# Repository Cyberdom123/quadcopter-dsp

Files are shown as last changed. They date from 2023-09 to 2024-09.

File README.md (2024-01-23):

# Quadcopter design made from scratch

The goal of the project is to create a working model of a quadcopter UAV, which can be
controlled with a Xbox controller. The project utilises the MPU6050 inertial measurement
unit, which combines MEMS accelerometer and gyroscope into a single IC. The combination of
sensor readings from the IMU combined with an adequate mathematical model and a regulating
system allows to make a quadcopter with a stable control system.



# Quadcopter project implementation

The MCU used in the project implementation is STM32F103C6T6, an ARM Cortex-M3 mi-
crocontroller, containing 32Kbytes of ROM. F1303 has built-in hardware support for I2C and
SPI busses used for data transmission between on-board peripherals.
The MPU6050 has been used as a sensor. It is an inertial measurement unit (IMU), a
MEMS integrated circuit combining in itself an accelerometer and a gyroscope. For easy and
intuitive reading of the sensor data at the code level, a library for initialising and handling the
MPU has been written. It uses the built-in I2C bus which is used to exchange data between the
IMU and MCU. The transmission is made in 400kHz mode. In order to save MCU execution
time, a DMA controller has been used, allowing for sending data from RAM to the peripheral.
Similarly, a library for nRF24L01 radio module has been written. nRF is being used for
digital radio transmission between the UAV and a PC. It is connected to the MCU by the
SPI bus and also uses the DMA mechanism. Another nRF connected to the PC is used to
communicate with the quadcopter. The transceivers are used in order to read telemetry data
and for piloting the UAV using an Xbox controller connected to the PC.

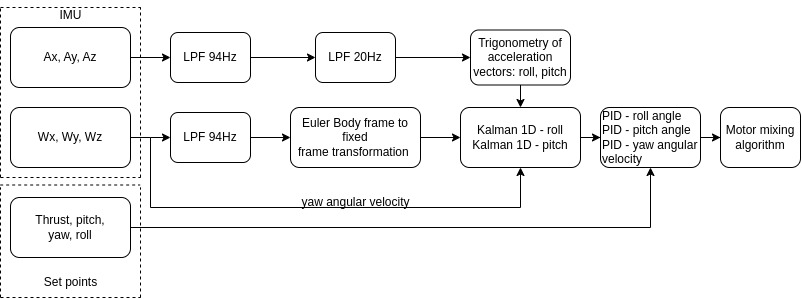
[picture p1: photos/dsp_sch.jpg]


To keep the UAV stable it is essential to keep it at a set (stable) angle during movement.
For instance, when we want the drone to fly up vertically, the roll and pitch angle have to be
set to 0 degrees. The IMU supplies the data about displacement and angular velocity and a
suitable mathematical model processes the data in order to estimate the angles.
Finally the integration of data from both sensors with the help of filtration algorithms,
such as complementary filter or Kalman filter allows us to gain precise information about
the angles and for effective stabilisation of the quadcopter during flight. In our project we
used the Kalman filter. It is an aimed at estimating the actual state of the system based
on the observer measurements with Gaussian noise. The algorithm works in two main steps:
estimation of the state of the system based on previous state and correcting it during the next
measurement. Kalman filter uses the mathematical model and data about Gaussian noise in
order to minimalise the estimates and measurement unceirtanties.
The angle estimates and yaw angular velocity is fed into the regulation system consisitng
of three PID regulators for every quantity. The PID regulator works by minimising the difference
between the actual state of the system and a desirable reference state. It contains three
components: proportional (P), which reacts proportionally to current deviateion, integral (I),
which accumulates the deviation as time passes and differential (D), which takes into account
the rate of change of the difference. The output of the PIDs is a duty cycle fed into a signal
mixer, which sets the duty cycle for each of the motors.

More detailed documentation has been placed in the project repository.

## Part list

- Frame: https://www.thingiverse.com/thing:1604440
- 7mm Motor Holder: https://www.thingiverse.com/thing:1675767
- 7x20mm 3.7V DC 46500RPM Motors CCW
- 7x20mm 3.7V DC 46500RPM Motors CW
- Propellers: 55mm
- Transceiver: 2.4GHz NRF24L01
- LiPo Battery: 520mAh 25C 12g Dualsky
- Gyroscope/Accelerometer: MPU6050
- Pressure Sensor: BMP280
- STM32-FC Board (located in the hardware folder)

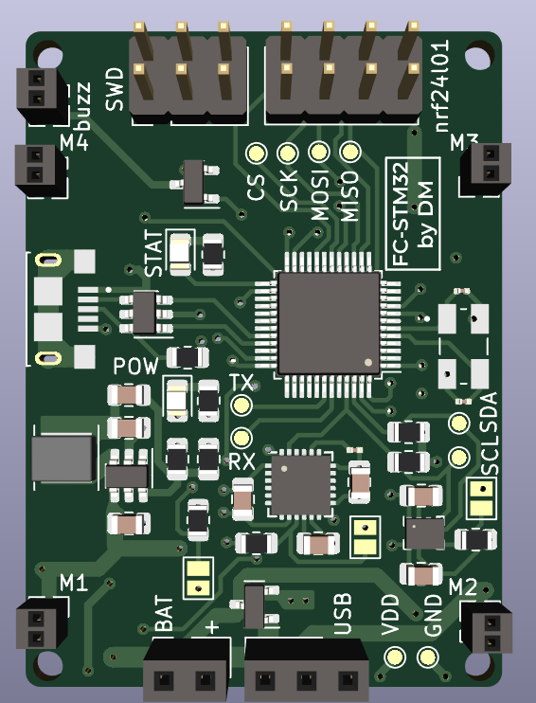
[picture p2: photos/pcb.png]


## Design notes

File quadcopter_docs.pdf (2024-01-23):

# Quadcopter Project documentation

### Dominik Michalczyk, Kacper Filipek

### January 2024

## 1. Project description

The goal of the project is to create a working model of a quadcopter UAV, which can be controlled with a Xbox controller. The project utilises the MPU6050 inertial measurement unit, which combines MEMS accelerometer and gyroscope into a single IC. The combination of sensor readings from the IMU combined with an adequate mathematical model and a regulating system allows to make a quadcopter with a stable control system.

## 2. Problem analysis

For the quadcopter to be stable, it needs to continuously measure the sensor data and estimate its attitute angles and correct to the set position and drive the motors in a way that reduces deviations from the user-set attitude.
Reading the sensor data is done by reading from specific registers of MPU6050. Adresses and descriptions of all registers are written in detail in the datasheet of the IC. A library for using IC must be written.
In order to control the drone, it needs to have a wireless communication circuit aboard. The nRF24 module allows for digital radio communication on 2.4GHz band.

## 3. Project implementation

The MCU used in the project implementation is STM32F103C6T6, an ARM Cortex-M3 microcontroller, containing 32Kbytes of ROM. F1303 has built-in hardware support for I²C and SPI busses used for data transmission between on-board peripherals.
The MPU6050 has been used as a sensor. It is an inertial measurement unit (IMU), a MEMS integrated circuit combining in itself an accelerometer and a gyroscope. For easy and intuitive reading of the sensor data at the code level, a library for initialising and handling the MPU has been written. It uses the built-in I²C bus which is used to exchange data between the IMU and MCU. The transmission is made in 400kHz mode. In order to save MCU execution time, a DMA controller has been used, allowing for sending data from RAM to the peripheral. Similarly, a library for nRF24L01 radio module has been written. nRF is being used for digital radio transmission between the UAV and a PC. It is connected to the MCU by the SPI bus and also uses the DMA mechanism. Another nRF connected to the PC is used to communicate with the quadcopter. The transceivers are used in order to read telemetry data and for piloting the UAV using an Xbox controller connected to the PC.

To keep the UAV stable it is essential to keep it at a set (stable) angle during movement. For instance, when we want the drone to fly up vertically, the roll and pitch angle have to be set to 0 degrees. The IMU supplies the data about displacement and angular velocity and a suitable mathematical model processes the data in order to estimate the angles.
Finally the integration of data from both sensors with the help of filtration algorithms, such as complementary filter or Kalman filter allows us to gain precise information about the angles and for effective stabilisation of the quadcopter during flight. In our project we used the Kalman filter. It is an aimed at estimating the actual state of the system based on the observer measurements with Gaussian noise. The algorithm works in two main steps: estimation of the state of the system based on previous state and correcting it during the next measurement. Kalman filter uses the mathematical model and data about Gaussian noise in order to minimalise the estimates and measurement unceirtanties.
The angle estimates and yaw angular velocity is fed into the regulation system consisitng of three PID regulators for every quantity. The PID regulator works by minimising the difference between the actual state of the system and a desirable reference state. It contains three components: proportional (P), which reacts proportionally to current deviateion, integral (I), which accumulates the deviation as time passes and differential (D), which takes into account the rate of change of the difference. The output of the PIDs is a duty cycle fed into a signal mixer, which sets the duty cicle for each of the motors.

## 4. Block diagrams

A simplified block diagram depicting the wiring of the circuit and its connection to PC

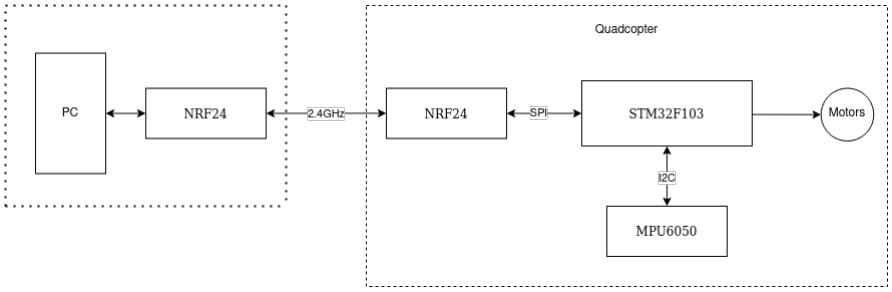
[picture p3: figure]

The code for reading the sensor data and motor regulation is made according to the block diagram below.


## 5. Code description

### 5.1. nrf24l01 library

- HAL StatusTypeDef NRF24L01 Init(NRF24L01 STRUCT *nrf24l01, NRF24L01 CONFIG *nrf24l01 cfg);
- Initializes the 2.4Ghz module and sets the default setting
- HAL StatusTypeDef NRF24L01 Enable ACKN Payload(NRF24L01
*nrf24l01);
- Enables acknowledge payloads support. Thanks to it, you can immediately send a message to the radio that previously transmitted the data.
- HAL StatusTypeDef NRF24L01 Open Reading Pipe(NRF24L01 STRUCT *nrf24l01, uint8 t pipeAddr, uint64 t rxAddr, uint8 t payloadSize);
- Opens a pipe through which messages from the transmitter will be received.
- HAL StatusTypeDef NRF24L01 Get Info(NRF24L01 STRUCT *nrf24l01);
- Reads all nrf24l01 status registers, used for debugging.
- HAL StatusTypeDef NRF24L01 Read PayloadDMA(NRF24L01 STRUCT
*nrf24l01, uint8 t len);
- Reads the payload sent by the transmitter using SPI in combination with the DMA (direct memory access controller).
- void NRF24L01 Read PayloadDMA Complete(NRF24L01 STRUCT
*nrf24l01, uint8 t *data, uint8 t len);
- After receiving data from the radio using DMA, it saves it to the given buffer.
- HAL StatusTypeDef NRF24L01 Write ACKN Payload(NRF24L01 STRUCT *nrf24l01, void *data, uint8 t len);
- Saves data that will be sent after receiving the next message from the transmitter.
- HAL StatusTypeDef NRF24L01 Start Listening(NRF24L01 STRUCT *nrf24l01);
- Starts listening for incoming packets and enables interrupts from nrf24l01.
- void NRF24L01 Stop Listening(NRF24L01 STRUCT *nrf24l01) - Stops listening for incoming packets and disables interrupts from nrf24l01.

### 5.2. rc library

- void RC Receive Message(uint8 t message[8], RC t *rc)
- Turns the received message into a control structure that is used to control the quadcopter

### 5.3. angle estimation library

- void Estimate Angles Init(float dt, float alpha, float tau)
- Initialize Angle estimator: dt - sampling time, alpha - coefficient for complementary filter, tau - coefficient for accelerometer lowpass filters, τ =

1
2πf .
- void Estimate Angles(float angles[2], float angular velocities[3],
float acc buf[3], float gyro buff[3])
- Calculates angles using trigonometry of acceleration vectors and transforms body frame to fixed frame using Euler rotation matrix. Finally, it combines these two readings using Kalman Filters or Complementary filters and thus estimates the angles at which the drone is located.

### 5.4. stabilizer library

- void Stabilizer init()
- Sets all PIDs and filters needed to stabilize the quadcopter.
- void Stabilize(float angles[2], float angular velocities[3], int8 t control inputs[4])
- Stabilizes the drone’s movement using PID controllers.

### 5.5. motors library

- void Motors SetPWR(uint8 t thrust, int8 t yaw, int8 t pitch, int8 t roll)
- Using the Motor Mixing Algorithm sets the pwm of all four motors.
- void Motors Switch(uint8 t power on)
- Turns the motors on and off.

### 5.6. MPU6050 library

- MPU6050 STRUCT - a structure tpye containing the I²C address of MPU6050 and addresses of buffers for the data being read.
- MPU6050 config - structure type for MPU configuration
- MPU6050 config MPU get default cfg(void) - returns the default configuration for MPU
- HAL StatusTypeDef MPU init(MPU6050 STRUCT *mpu, MPU6050 config* cfg) - initialises the MPU according to the config passed as argument.
- HAL StatusTypeDef MPU measure gyro offset(MPU6050 STRUCT* mpu, uint16 t samples
- measures the constant offset of the gyroscope based on set sample number.
- HAL StatusTypeDef MPU measure acc offset(MPU6050 STRUCT* mpu, uint16 t samples)
- measures the constant offset of the accelerometer.
- HAL StatusTypeDef MPU clear int(MPU6050 STRUCT *mpu) - clears the interrup flag from MPU’s interrupt status register.
- HAL StatusTypeDef MPU read acc gyro DMA(MPU6050 STRUCT *mpu) - reads accelerometer and gyroscope data using DMA to a memory location passed using the config struct.
- HAL StatusTypeDef MPU read acc gyro DMA complete(MPU6050 STRUCT *mpu) - calculates the sensor values from raw bytes after the readout has been completed.

Note that the functions for measuring the offsets write the result to a static variable defined in the library source file. The functions for reading the measurements of the IMU substract the offsets automatically.

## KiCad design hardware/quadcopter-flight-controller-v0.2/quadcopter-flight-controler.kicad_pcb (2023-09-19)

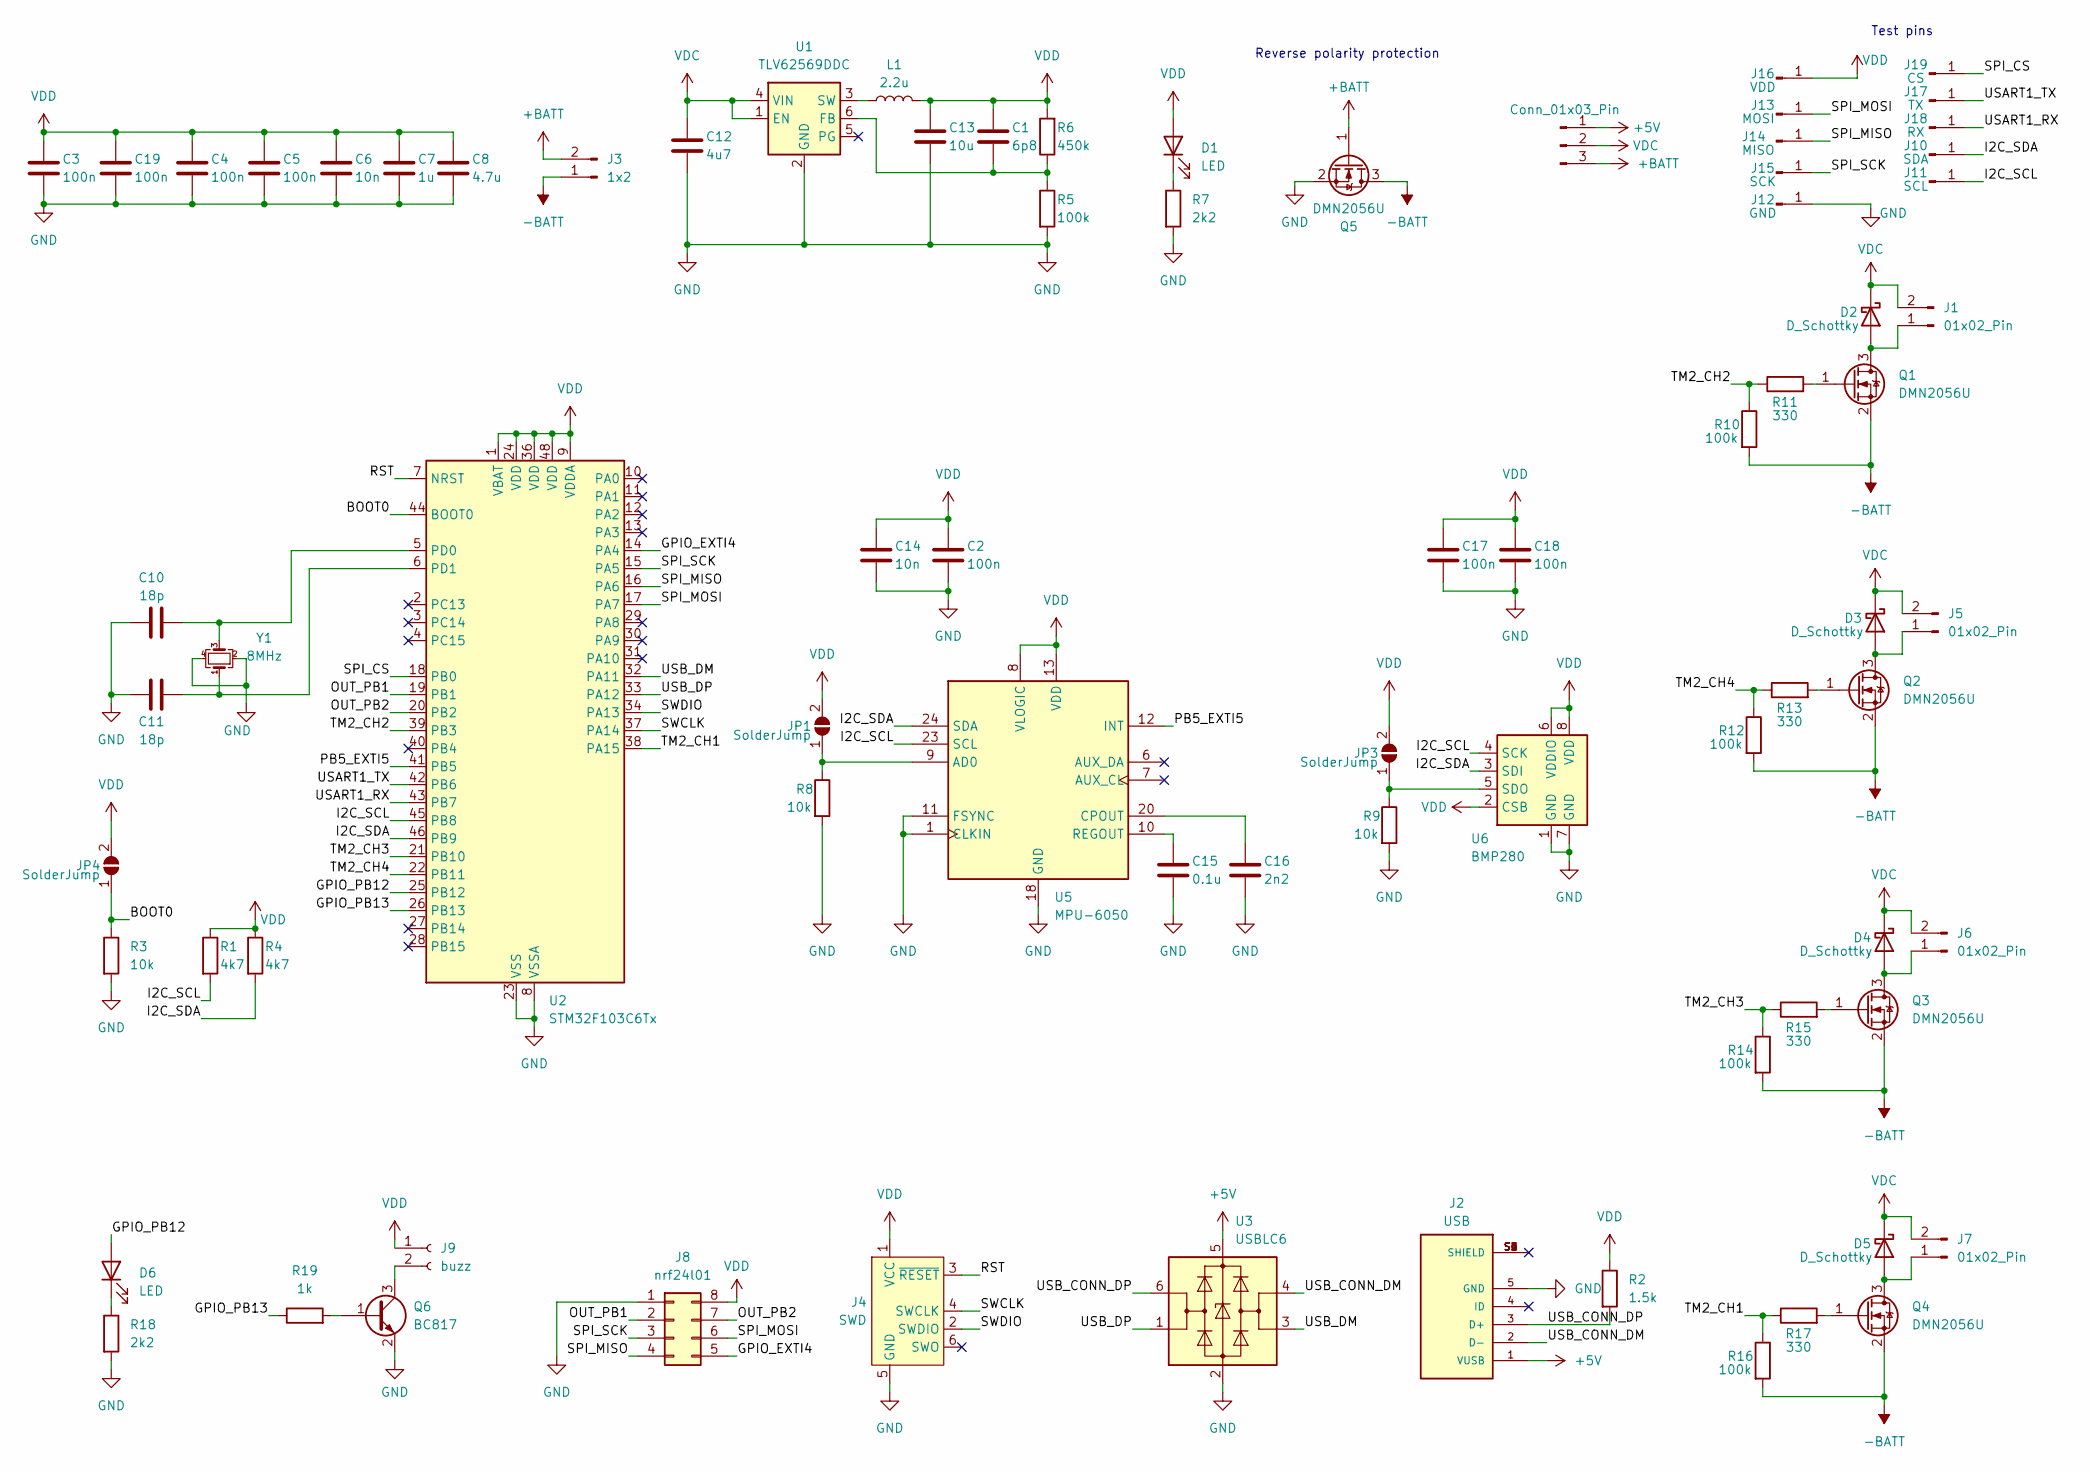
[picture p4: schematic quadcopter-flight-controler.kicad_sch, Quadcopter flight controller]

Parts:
C1: 6p8; C_0805_2012Metric
C2, C3, C4, C5, C17, C18, C19: 100n; C_0805_2012Metric
C6, C14: 10n; C_0805_2012Metric
C7: 1u; C_0805_2012Metric
C8: 4.7u; C_1206_3216Metric
C10, C11: 18p; C_0201_0603Metric
C12: 4u7; C_0805_2012Metric
C13: 10u; C_0805_2012Metric
C15: 0.1u; C_0805_2012Metric
C16: 2n2; C_0201_0603Metric
D1, D6: LED; LED_0805_2012Metric
D2, D3, D4, D5: D_Schottky; D_SOD-123F
J1, J5, J6, J7: 01x02_Pin; PinSocket_1x02_P1.27mm_Vertical
J2: USB; AMPHENOL_10118193-0001LF; PARTREV E
J3: 1x2; PinSocket_1x02_P2.54mm_Vertical
J4: SWD; Pin_2x03_P2.54mm
J8: nrf24l01; PinHeader_2x04_P2.54mm_Vertical
J9: buzz; PinSocket_1x02_P1.27mm_Vertical
J10: SDA; TestPoint_Pad_D1.0mm
J11: SCL; TestPoint_Pad_D1.0mm
J12: GND; TestPoint_Pad_D1.0mm
J13: MOSI; TestPoint_Pad_D1.0mm
J14: MISO; TestPoint_Pad_D1.0mm
J15: SCK; TestPoint_Pad_D1.0mm
J16: VDD; TestPoint_Pad_D1.0mm
J17: TX; TestPoint_Pad_D1.0mm
J18: RX; TestPoint_Pad_D1.0mm
J19: CS; TestPoint_Pad_D1.0mm
J20: Conn_01x03_Pin; PinSocket_1x03_P2.54mm_Vertical
JP1, JP3, JP4: SolderJump; SolderJumper-2_P1.3mm_Open_Pad1.0x1.5mm
L1: 2.2u; L_Coilcraft_XxL4040
Q1, Q2, Q3, Q4, Q5: DMN2056U; SOT-23
Q6: BC817; SOT-23
R1, R4: 4k7; R_0805_2012Metric
R2: 1.5k; R_0805_2012Metric
R3, R8, R9: 10k; R_0805_2012Metric
R5, R10, R12, R14, R16: 100k; R_0805_2012Metric
R6: 450k; R_0805_2012Metric
R7, R18: 2k2; R_0805_2012Metric
R11, R13, R15, R17: 330; R_0805_2012Metric
R19: 1k; R_0805_2012Metric
U1: TLV62569DDC; SOT-23-6
U2: STM32F103C6Tx; LQFP-48_7x7mm_P0.5mm
U3: USBLC6; SOT-23-6
U5: MPU-6050; InvenSense_QFN-24_4x4mm_P0.5mm
U6: BMP280; Bosch_LGA-8_2x2.5mm_P0.65mm_ClockwisePinNumbering
Y1: 8MHz; XTAL_QT532S-8.000MAAJ-T

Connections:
+5V: J2.1 (VUSB), J20.1, U3.5 (VBUS)
+BATT: J3.2, J20.3, Q5.1 (G)
-BATT: J3.1, Q1.2 (S), Q2.2 (S), Q3.2 (S), Q4.2 (S), Q5.3 (D), R10.2, R12.2, R14.2, R16.2
/BOOT0: JP4.1 (A), R3.1, U2.44 (BOOT0)
/GPIO_EXTI4: J8.5, U2.14 (PA4)
/GPIO_PB12: D6.2 (A), U2.25 (PB12)
/GPIO_PB13: R19.1, U2.26 (PB13)
/I2C_SCL: J11.1, R1.2, U2.45 (PB8), U5.23 (SCL), U6.4 (SCK)
/I2C_SDA: J10.1, R4.2, U2.46 (PB9), U5.24 (SDA), U6.3 (SDI)
/OUT_PB1: J8.2, U2.19 (PB1)
/OUT_PB2: J8.7, U2.20 (PB2)
/PB5_EXTI5: U2.41 (PB5), U5.12 (INT)
/RST: J4.3 (~RESET), U2.7 (NRST)
/SPI_CS: J19.1, U2.18 (PB0)
/SPI_MISO: J8.4, J14.1, U2.16 (PA6)
/SPI_MOSI: J8.6, J13.1, U2.17 (PA7)
/SPI_SCK: J8.3, J15.1, U2.15 (PA5)
/SWCLK: J4.4 (SWCLK), U2.37 (PA14)
/SWDIO: J4.2 (SWDIO), U2.34 (PA13)
/TM2_CH1: R16.1, R17.1, U2.38 (PA15)
/TM2_CH2: R10.1, R11.1, U2.39 (PB3)
/TM2_CH3: R14.1, R15.1, U2.21 (PB10)
/TM2_CH4: R12.1, R13.1, U2.22 (PB11)
/USART1_RX: J18.1, U2.43 (PB7)
/USART1_TX: J17.1, U2.42 (PB6)
/USB_CONN_DM: J2.2 (D-), U3.4 (I/O2)
/USB_CONN_DP: J2.3 (D+), R2.2, U3.6 (I/O1)
/USB_DM: U2.32 (PA11), U3.3 (I/O2)
/USB_DP: U2.33 (PA12), U3.1 (I/O1)
GND: C2.2, C3.2, C4.2, C5.2, C6.2, C7.2, C8.2, C10.1, C11.1, C12.2, C13.2, C14.2, C15.2, C16.2, C17.2, C18.2, C19.2, J2.5 (GND), J4.5 (GND), J8.1, J12.1, Q5.2 (S), Q6.2 (E), R3.2, R5.2, R7.2, R8.2, R9.2, R18.2, U1.2 (GND), U2.8 (VSSA), U2.23 (VSS), U2.35 (VSS), U2.47 (VSS), U3.2 (GND), U5.1 (CLKIN), U5.11 (FSYNC), U5.18 (GND), U6.1 (GND), U6.7 (GND), Y1.2, Y1.4
unnamed: D1.1 (K), R7.1
unnamed: D2.2 (A), J1.1, Q1.3 (D)
unnamed: D3.2 (A), J5.1, Q2.3 (D)
unnamed: D4.2 (A), J6.1, Q3.3 (D)
unnamed: D5.2 (A), J7.1, Q4.3 (D)
unnamed: D6.1 (K), R18.1
unnamed: J9.2, Q6.3 (C)
unnamed: JP1.1 (A), R8.1, U5.9 (AD0)
unnamed: JP3.1 (A), R9.1, U6.5 (SDO)
unnamed: Q1.1 (G), R11.2
unnamed: Q2.1 (G), R13.2
unnamed: Q3.1 (G), R15.2
unnamed: Q4.1 (G), R17.2
unnamed: Q6.1 (B), R19.2
unnamed: C1.2, R5.1, R6.1, U1.6 (FB)
unnamed: L1.1, U1.3 (SW)
unnamed: C10.2, U2.5 (PD0), Y1.3
unnamed: C11.2, U2.6 (PD1), Y1.1
unnamed: C16.1, U5.20 (CPOUT)
unnamed: C15.1, U5.10 (REGOUT)
VDC: C12.1, D2.1 (K), D3.1 (K), D4.1 (K), D5.1 (K), J1.2, J5.2, J6.2, J7.2, J20.2, U1.1 (EN), U1.4 (VIN)
VDD: C1.1, C2.1, C3.1, C4.1, C5.1, C6.1, C7.1, C8.1, C13.1, C14.1, C17.1, C18.1, C19.1, D1.2 (A), J4.1 (VCC), J8.8, J9.1, J16.1, JP1.2 (B), JP3.2 (B), JP4.2 (B), L1.2, R1.1, R2.1, R4.1, R6.2, U2.1 (VBAT), U2.9 (VDDA), U2.24 (VDD), U2.36 (VDD), U2.48 (VDD), U5.8 (VLOGIC), U5.13 (VDD), U6.2 (CSB), U6.6 (VDDIO), U6.8 (VDD)

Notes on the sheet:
Test pins
Reverse polarity protection

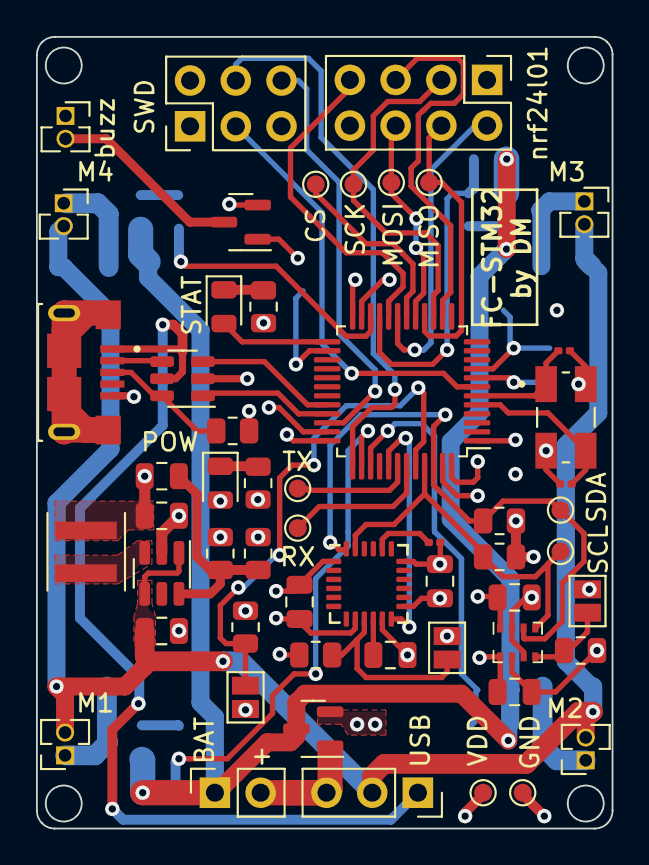
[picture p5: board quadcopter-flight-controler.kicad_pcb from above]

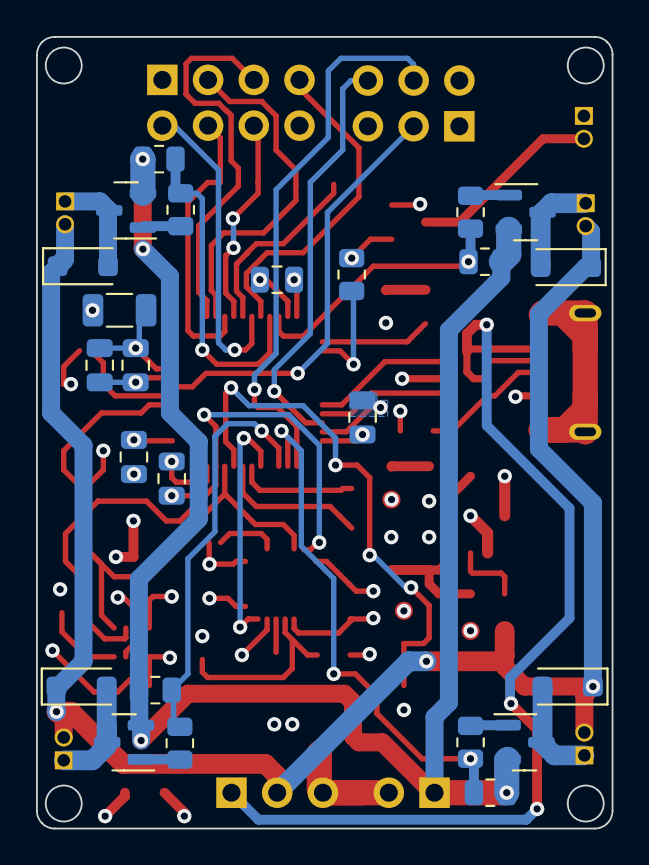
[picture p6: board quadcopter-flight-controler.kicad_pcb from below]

Board: 4 copper layers, 32.0 x 44.0 mm, 79 parts (24 on the bottom side), 52 nets.

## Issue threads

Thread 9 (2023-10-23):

Add system for loggin the sensor data in SPI flash

kflpk, 2023-10-23:
Sensor data is to be logged for post-hoc analysis of filters and other DSP systems in the drone

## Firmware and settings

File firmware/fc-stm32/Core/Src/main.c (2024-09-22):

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
/* Includes ------------------------------------------------------------------*/
#include "main.h"
#include "dma.h"
#include "gpio.h"
#include "i2c.h"
#include "spi.h"
#include "tim.h"
#include "usart.h"

/* USER CODE BEGIN Includes */
#include "flight_controller.h"
/* USER CODE END Includes */

/* USER CODE BEGIN PTD */
// #define TELEMETRY
/* USER CODE END PTD */


void SystemClock_Config(void);
/* USER CODE BEGIN 0 */
void HAL_I2C_MemRxCpltCallback(I2C_HandleTypeDef *hi2c) {
    (void)hi2c;

#ifdef HAL_RADIO_INTERFACE_I2C
    HAL_RADIO_receive_payload();
#endif // RADIO_INTERFACE_I2C

#ifdef HAL_IMU_INTERFACE_I2C
    HAL_IMU_readout();
#endif // IMU_INTERFACE_I2C
}

void HAL_SPI_TxRxCpltCallback(SPI_HandleTypeDef *hspi) {
    (void)hspi;

#ifdef HAL_RADIO_INTERFACE_SPI
    HAL_RADIO_receive_payload();
#endif // RADIO_INTERFACE_SPI

#ifdef HAL_IMU_INTERFACE_SPI
    HAL_IMU_readout();
#endif // IMU_INTERFACE_SPI

#ifdef HAL_EXTERNAL_MEMORY_INTERFACE_SPI
    HAL_EXTERNAL_MEMORY_readout();
#endif // EXTERNAL_MEMORY_INTERFACE_SPI
}

void HAL_GPIO_EXTI_Callback(uint16_t GPIO_Pin) {
    if (GPIO_Pin == RADIO_INT_Pin) {
        HAL_RADIO_request_readout();
    }
    if (GPIO_Pin == IMU_INT_Pin) {
        HAL_IMU_request_readout();
    }
}
/* USER CODE END 0 */

/**
 * @brief  The application entry point.
 * @retval int
 */
int main(void) {

    /* MCU
     * Configuration--------------------------------------------------------*/

    /* Reset of all peripherals, Initializes the Flash interface and the
     * Systick. */
    HAL_Init();

    /* Configure the system clock */
    SystemClock_Config();

    /* Initialize all configured peripherals */
    MX_GPIO_Init();
    MX_DMA_Init();
    MX_SPI1_Init();
    MX_TIM1_Init();
    MX_I2C1_Init();
    MX_TIM2_Init();
    MX_USART1_UART_Init();
    /* USER CODE BEGIN 2 */
    FC_init();
    /* USER CODE END 2 */

    /* Infinite loop */
    /* USER CODE BEGIN WHILE */
    while (1) {
        FC_proc();
    }
    /* USER CODE END WHILE */

}

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


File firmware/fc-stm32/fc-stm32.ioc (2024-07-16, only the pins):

Mcu.UserName=STM32F103C6Tx
PA13.Signal=SYS_JTMS-SWDIO
PA14.Signal=SYS_JTCK-SWCLK
PA15.Signal=S_TIM2_CH1_ETR
PA4.GPIO_Label=NRF_INT
PA4.Signal=GPXTI4
PA5.Signal=SPI1_SCK
PA6.Signal=SPI1_MISO
PA7.Signal=SPI1_MOSI
PB0.GPIO_Label=SPI_CS
PB0.Signal=GPIO_Output
PB1.GPIO_Label=CSN
PB1.Signal=GPIO_Output
PB10.Signal=S_TIM2_CH3
PB11.Signal=S_TIM2_CH4
PB12.GPIO_Label=STATUS_LED
PB12.Signal=GPIO_Output
PB2.GPIO_Label=CE
PB2.Signal=GPIO_Output
PB3.Signal=S_TIM2_CH2
PB5.GPIO_Label=MPU_INT
PB5.Signal=GPXTI5
PB6.Signal=USART1_TX
PB7.Signal=USART1_RX
PB8.Signal=I2C1_SCL
PB9.Signal=I2C1_SDA
PD0-OSC_IN.Signal=RCC_OSC_IN
PD1-OSC_OUT.Signal=RCC_OSC_OUT

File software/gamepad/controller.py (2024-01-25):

from inputs import get_gamepad
import serial
import struct
import time
import math
import threading
import numpy as np

from logger import DataLogger

ser = serial.Serial('/dev/ttyUSB0', 57600)

class XboxController(object):
    MAX_TRIG_VAL = math.pow(2, 8)
    MAX_JOY_VAL = math.pow(2, 15)

    def __init__(self):

        self.dataLogger = DataLogger("flight5.csv")

        self.LeftJoystickY = 0
        self.LeftJoystickX = 0
        self.RightJoystickY = 0
        self.RightJoystickX = 0
        self.LeftTrigger = 0
        self.RightTrigger = 0
        self.LeftBumper = 0
        self.RightBumper = 0
        self.A = 0
        self.X = 0
        self.Y = 0
        self.B = 0
        self.LeftThumb = 0
        self.RightThumb = 0
        self.Back = 0
        self.Start = 0
        self.LeftDPad = 0
        self.RightDPad = 0
        self.UpDPad = 0
        self.DownDPad = 0

        self._monitor_thread = threading.Thread(target=self._monitor_controller, args=())
        self._monitor_thread.daemon = True
        self._monitor_thread.start()


    def read(self): # return the buttons/triggers that you care about in this methode
        x = self.LeftJoystickX
        y = self.LeftJoystickY
        a = self.A
        return [x, y, a]
    
    def send(self):
        x1 = np.uint8(np.int8(-round(self.LeftJoystickX*100)))
        y1 = np.uint8(np.int8(-round(self.LeftJoystickY*100)))
        x2 = np.uint8(np.int8(-round(self.RightJoystickX*100)))
        y2 = np.uint8(np.int8(round(self.RightJoystickY*100)))
        a = self.A
        b = self.B

        #time.sleep(0.0001)
        ser.write(bytearray([y1, y2, 0, x2, a, b]))
        #print(y1, 0, x2, y2, a, b)
        msg = ser.read(24)

        try:
            [acc0, acc1, acc2, gyro0, gyro1, gyro2] = struct.unpack('6f', msg)
            self.dataLogger.log_data(acc0, acc1, acc2, gyro0, gyro1, gyro2)
            print(f"{acc0:7.2f} {acc1:7.2f} {acc2:7.2f} {gyro0:7.2f} {gyro1:7.2f} {gyro2:7.2f}", end="\r")
        except:
            pass

    def _monitor_controller(self):
        while True:
            events = get_gamepad()
            for event in events:
                if event.code == 'ABS_Y':
                    self.LeftJoystickY = event.state / XboxController.MAX_JOY_VAL # normalize between -1 and 1
                elif event.code == 'ABS_X':
                    self.LeftJoystickX = event.state / XboxController.MAX_JOY_VAL # normalize between -1 and 1
                elif event.code == 'ABS_RY':
                    self.RightJoystickY = event.state / XboxController.MAX_JOY_VAL # normalize between -1 and 1
                elif event.code == 'ABS_RX':
                    self.RightJoystickX = event.state / XboxController.MAX_JOY_VAL # normalize between -1 and 1
                elif event.code == 'ABS_Z':
                    self.LeftTrigger = event.state / XboxController.MAX_TRIG_VAL # normalize between 0 and 1
                elif event.code == 'ABS_RZ':
                    self.RightTrigger = event.state / XboxController.MAX_TRIG_VAL # normalize between 0 and 1
                elif event.code == 'BTN_TL':
                    self.LeftBumper = event.state
                elif event.code == 'BTN_TR':
                    self.RightBumper = event.state
                elif event.code == 'BTN_SOUTH':
                    self.A = event.state
                elif event.code == 'BTN_NORTH':
                    self.Y = event.state #previously switched with X
                elif event.code == 'BTN_WEST':
                    self.X = event.state #previously switched with Y
                elif event.code == 'BTN_EAST':
                    self.B = event.state
                elif event.code == 'BTN_THUMBL':
                    self.LeftThumb = event.state
                elif event.code == 'BTN_THUMBR':
                    self.RightThumb = event.state
                elif event.code == 'BTN_SELECT':
                    self.Back = event.state
                elif event.code == 'BTN_START':
                    self.Start = event.state
                elif event.code == 'BTN_TRIGGER_HAPPY1':
                    self.LeftDPad = event.state
                elif event.code == 'BTN_TRIGGER_HAPPY2':
                    self.RightDPad = event.state
                elif event.code == 'BTN_TRIGGER_HAPPY3':
                    self.UpDPad = event.state
                elif event.code == 'BTN_TRIGGER_HAPPY4':
                    self.DownDPad = event.state


if __name__ == '__main__':
    joy = XboxController()
    ser.timeout = 1
    while True:
        try:
            joy.send()
        except KeyboardInterrupt:
            print(" Nara")
            #joy.dataLogger.save_data()
            exit()

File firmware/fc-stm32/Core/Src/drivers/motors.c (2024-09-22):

/**
 * @file motors.c
 * @author Dominik Michalczyk
 * @brief 
 * @version 0.1
 * @date 2024-01-26
 */

#include "drivers/motors.h"

#include "gpio.h"
#include "tim.h"

#include <stdbool.h>
#include <stdint.h>

void Motors_Run(int8_t thrust, int8_t yaw, int8_t pitch, int8_t roll, bool power_on){
    Motors_SetPWR(thrust, yaw, pitch, roll);
    Motors_Switch(power_on);
}

void Motors_Switch(bool power_on){
  if(power_on){
    //Start all PWM chanels
    HAL_TIM_PWM_Start(&htim2, TIM_CHANNEL_1);
    HAL_TIM_PWM_Start(&htim2, TIM_CHANNEL_2);
    HAL_TIM_PWM_Start(&htim2, TIM_CHANNEL_3);
    HAL_TIM_PWM_Start(&htim2, TIM_CHANNEL_4);   
  }else{
    //Stop all PWM chanels
    HAL_TIM_PWM_Stop(&htim2, TIM_CHANNEL_1);
    HAL_TIM_PWM_Stop(&htim2, TIM_CHANNEL_2);
    HAL_TIM_PWM_Stop(&htim2, TIM_CHANNEL_3);
    HAL_TIM_PWM_Stop(&htim2, TIM_CHANNEL_4);
  }
}

void Motors_SetPWR(uint8_t thrust, int8_t yaw, int8_t pitch, int8_t roll)
{
  //Motor 1 PWM duty cycle
  TIM2->CCR1 = THRUST_CONST * thrust - PITCH_CONST * pitch + YAW_CONST * yaw - ROLL_CONST * roll;
  //Motor 2 PWM duty cycle
  TIM2->CCR2 = THRUST_CONST * thrust + PITCH_CONST * pitch - YAW_CONST * yaw - ROLL_CONST * roll;
  //Motor 3 PWM duty cycle
  TIM2->CCR3 = THRUST_CONST * thrust + PITCH_CONST * pitch + YAW_CONST * yaw + ROLL_CONST * roll;
  //Motor 4 PWM duty cycle
  TIM2->CCR4 = THRUST_CONST * thrust - PITCH_CONST * pitch - YAW_CONST * yaw + ROLL_CONST * roll;
}

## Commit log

2023-08-12 new pcb
    [flight-controller-simulation.kicad_sch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]
2023-09-14 nrf24-lib, stm32-fc-tests
    [flight-controller-simulation.kicad_sch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]
2023-09-19 some tests
    [quadcopter-flight-controler.kicad_pcb]
2023-09-19 moved tests to `firmware/tests`; moved main firmware to `firmware`; added `software` folder
    [flight-controller-simulation.kicad_sch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]
2023-09-25 Radio control improvement
    * rc
    * controller_script_improvements
    * interrupt fix
    * device power down
    * prettier comments
    * Spi transmit-recieve implementation
    * SPI DMA
    * removing .vscode
    * fixing .vscode
    [controller.py, fc-stm32.ioc, main.c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]
2023-09-28 added the register map, corrected some register names
    [mpu6050.c, mpu6050.h]
2023-10-03 nrf_cfg struct, motors.h
2023-10-04 changed implementation od MPU_init to use resolution setters; fixed a bug, where acc and gyro reads returned wrong values
    [main.c, mpu6050.c, mpu6050.h]
2023-10-04 fixed typo in enum
    [mpu6050.h]
2023-10-09 pid implementation
2023-10-16 Ack npayload (#8)
    * successfully enabled ack payload
    * fixed bugs
    * removed .vscode
    [fc-stm32.ioc, main.c, nrf24l01.c]
2023-10-18 python filters simulations
2023-10-20 added rudimentary EMA filter, not tested yet
2023-10-23 Added support for DMA in MPU6050 driver, yet to be tested
2023-10-31 added interrupts tests
2023-11-22 accelerometer pitch, roll estimation
2023-11-22 filter tests, logged sample data from accelerometer
2023-11-26 hardware low-pass filter enabled
2023-12-06 additional filtering added
2023-12-09 Control loop test with complementary filter
2023-12-14 IIR filters calculations
2023-12-19 filter design
2023-12-21 band pass filter calculations
2023-12-21 added some filter prototypes
2023-12-26 Logger (#13)
    * spi flash logger
    * logger interface
2023-12-26 first working prototype
2024-01-01 added low pass filter
    [flight1.csv, flight2.csv, flight4.csv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]
2024-01-02 one dimensional kalman filter
2024-01-04 the stabilization algorithm now uses a kalman filter
    [flight5.csv]
2024-01-25 fixed bugs, added flash_memory lib, imporved controller script
    [controller.py, flash_memory.c, main.c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]
2024-01-25 added missing files (rc-timeout, linker)
    [main.c]
2024-01-26 added missing files descriptions
    [flash_memory.c, motors.c, mpu6050.c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]
2024-02-27 Cmake build sys (#16)
    * added CmakeLists.txt
    * ld issue
    * replaced build system with cmake
    * added makeflie
    * vscode cfg
    * eanbled debugging with openOCD and gdb
    [fc-stm32.ioc]
2024-07-16 ibus driver
2024-08-04 FIX: MPU wrong address
    [mpu6050.h]
2024-09-17 extended stm32 hal library
2024-09-22 add 0s flag to debug build, moved interrupts handlers to main
2024-11-09 refine PID parameters

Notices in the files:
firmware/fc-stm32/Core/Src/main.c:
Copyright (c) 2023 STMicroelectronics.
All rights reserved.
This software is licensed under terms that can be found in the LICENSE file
